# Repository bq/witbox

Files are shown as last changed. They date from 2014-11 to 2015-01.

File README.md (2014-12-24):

Witbox
======

In this repository you will find the source files for the [bq Witbox 3D printer](http://www.bq.com/es/productos/witbox.html). If you are missing something, please do not hesitate to [file an issue on github](https://github.com/bq/witbox/issues).

# License 

Witbox is licensed under a [Creative Commons Attribution-ShareAlike 4.0 International License](http://creativecommons.org/licenses/by-sa/4.0/)

Please read the LICENSE file for more details.

Directory structure
===================

 * `autodesk-inventor`: The original Witbox source files for Autodesk Inventor(tm) and the exported step file. This folder is frozen. Find the latest version in the `freecad` folder

 * `freecad`: Witbox source files in [FreeCAD](http://www.freecadweb.org/). This is a work in progress. All the original files are being migrated to Freecad (see below)

 * `Witbox-BOM.ods`: Witbox Bill of Materials. Document for [LibreOffice](https://www.libreoffice.org/).

**Please note**: The original Witbox design was made in Autodesk Inventor(tm) which is proprietary software. Since we love open formats we are migrating the Witbox parts to [FreeCAD](http://www.freecadweb.org/), which is a multiplatform open source CAD software. We invite people from the community to join us and help us to complete the task.

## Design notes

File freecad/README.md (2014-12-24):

Open Format
===========

In this repository you will find the source files of the [bq witbox 3D printer](http://www.bq.com/gb/products/witbox.html) migrated to [FreeCAD](http://www.freecadweb.org/). This migration is an ongoing work in progress, but if you are missing something specific, please do not hesitate to [file an issue on github](https://github.com/bq/witbox/issues).

Directory structure
===================

There are two folders:

* `native-freecad`: contains the Witbox parts in FreeCAD's native .fcstd format
* `exports`: contains exports of the parts generated from the FreeCAD source files
  * `stl`: Parts exported to STL format
  * `step`: Parts exported to STEP format

Work in progress
================

We are migrating the Witbox parts from Autodesk Inventor to FreeCAD. Currently only a few parts have been migrated. We invite people from the community to join us and help us to complete the task.

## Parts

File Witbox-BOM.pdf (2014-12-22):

## Witbox BOM

Part Number | Description | Quantity | Units | Comments
C04H030029 | XY Support | 1 PCs | | 2mm metal sheet
C04H020006 | Bearing MF105zz (5x10x4) | 8 PCs
C04H030014 | Rear rod drive Ø5 – 487mm | 1 PCs
C04H030017 | Front rod drive Ø5 – 50mm | 2 PCs
C04H020003 | GT2 Pulley 20 teeth | 7 PCs
C04H020014 | Y Belt -- GT2 2MR-280 | 1 PCs
C04H020015 | Y Belt -- GT2 2MR-696 | 2 PCs
C04H010011 | Nema17 Motor, 12VDC, 4000g.cm | 3 PCs | | PTFE
C04H030034 | X Motor Support | 1 PCs | | 3mm metal sheet
C04H030030 | X carriage | 1 PCs | | 2mm metal sheet
C04H030031 | X-end-motor | 1 PCs | | 2mm metal sheet
C04H030032 | X-end | 1 PCs | | 2mm metal sheet
05BQMEC005 | Linear Ball Bearing LM8uu | 8 PCs
C04H010003 | Mechanical Endstop | 3 PCs | | x,y and z axes
C04H030023 | Plastic Support Endstop | 3 PCs
C04H020027 | X-Ends Chain pair | 1 PCs | | (male and female ends)
C04H020029 | Y-Ends Chain pair | 1 PCs | | (male and female ends)
C04H030015 | Y smooth rod Ø8 – 360mm | 2 PCs
C04H030016 | X smooth rod Ø8 – 380mm | 2 PCs
C04H020016 | X Belt-GT2 2MR-848 | 1 PCs
C04H030019 | X-axis idler pulley | 1 PCs
C04H030018 | X-axis idler pulley shaft | 1 PCs
C04H030012 | X-axis idler pulley support | 1 PCs
C04A100003 | Witbox extruder sticker | 1 PCs
C04H050002 | Setscrew M4x5 ISO 4026/DIN-913 | 19 PCs | | Pulleys, linear bearings
C04H050009 | Bolt M4 x 6 DIN 7984 | 34 PCs
C04H050017 | Bolt M3 x 6 ISO 7380 | 23 PCs
G003286 | Led strip with wires | 1 PCs
C04H040005 | Pneumatic tube Ø8 | 0.079 m | | 3 parts (covers for drive bars)
C04H030024 | Air nozzle | 1 PCs | | PLA printed part
C04H020035 | MK7 Drive Gear for 1.75mm | 1 PCs
C04H030009 | Lever extruder | 1 PCs
C04H020008 | Bearing 623ZZ (3x10x4) | 1 PCs
C04H040004 | PTFE Tube Ø4 | 0.02 m | | Hotend
C04H010008 | B57560G104F 100k Thermistor | 1 PCs
C04H010033 | 40w Ceramic Cartridge Heater | 1 PCs
C04H030096 | Extruder motor support | 1 PCs
C04H020019 | Extruder spring 16mm Ø4 Ø0.6 | 1 PCs
C04H020001 | Extruder Heat Sink (40x40x11) | 1 PCs
C04H010006 | Brushless DC Cooling Fan - RD4010B12H | 1 PCs
C04H030033 | Blower support | 1 PCs | | 2mm metal sheet
C04H010007 | DC Blower Fan RB5015B12M+ 40 mm wire – JST male connector 2.5mm pitch | 1 PCs
C04H040001 | Rotatory Pneumatic fitting | 1 PCs
C04H030010 | Fibonacci Support | 1 PCs
C04H040002 | Pneumatic fitting QSMS-4 | 1 PCs
C04H050001 | Setscrew M3x4 ISO 4026/DIN-913 | 3
C04H050004 | dowel pin Ø3x20 – ISO-2338/DIN-7 | 1 PCs
C04H050005 | Bolt M3x12 – ISO-10642/DIN-7991 | 1 PCs
C04H050007 | Bolt M3x6 – ISO-10642/DIN-7991 | 42 PCs
C04H050009 | Bolt M4 x 6 DIN 7984 | 6 PCs
C04H050012 | Bolt M3x14 - ISO- 4762/DIN-912 | 1 PCs
C04H050013 | Bolt M3x18 - ISO- 4762/DIN-912 | 2 PCs

C04H050014 | Bolt M3x20 - ISO- 4762/DIN-912 | 2 PCs
C04H050015 | Bolt M3x22 - ISO- 4762/DIN-912 | 4 PCs
C04A010001 | Black Strap 50X2.5x190 | 2 PCs
C04H040003 | PTFE tube | 1.38 m | Fibonacci
G003287 | Cable chain | 1
C04H030022 | Fitting ferrule | 1 PCs
C04H030045 | Metal sheet base 1.5mm | 1 PCs
C04H010010 | Power Supply S350-12 AC | 1 PCs
C04H010014 | BULGIN BZM27/Z0000/57B | 1 PCs
C04H010002 | Smart LCD controller | 1 PCs
G004085 | Display Housing | 1 PCs
C04H010005 | Brushless DC Cooling Fan – RD5010B12H | 2 PCs
C04H030046 | Electronic metal sheet cover 1.5mm | 1 PCs
C04H010001 | Ramps 1.4 Kit | 1 PCs
C04H010020 | Stepstick Drivers A49988 4 layers | 4 PCs
C04H030013 | Control Knob | 1 PCs
C04H020013 | Hinge | 2 PCs
C04H030047 | Hinge supplement | 2 PCs
C04H050003 | Setscrew M5x8 Iso - 4026/Din - 913 | 1 PCs | Control Knob
C05I070037 | M8x20 Screw ISO 7380 - ZN | 2 PCs
C04H050022 | M4.2 x 16 ISO 7380 | 4 PCs
C04H050025 | M5 Nut DIN-934 | 8 PCs
C04H050021 | Screw 2.9 x 8 | 4 PCs
C04H030057 | Plastic Support Fan 50 | 2 PCs
C04H030026 | Arduino plastic base | 1 PCs
C04H030040 | Left Corner Metal Sheet | 1 PCs
C04H010012 | Nema17 Motor, 12VDC, 4800g.cm | 1 PCs | Y axis
C04H030035 | Y Motor support | 1 PCs | 3mm metal sheet
C04H020009 | Flexible Shaft Z Coupling 5mm/8mm | 1 PCs
C04H030048 | Motor Z support | 1 PCs | 3mm metal sheet
C04H020024 | Lead Screw Z Axis 2mm pitch | 1 PCs
C04H020023 | Screw Drive SWZ-W-104003 | 1 PCs
C04H030036 | Y Mechanical Endstop Support | 1 PCs
C04H030081 | Bed metal support | 1 PCs | 2mm metal sheet
C04H030041 | Z carriage | 1 PCs | 2mm metal sheet
C04H020018 | Spring Ø6 Ø0.8 30mm | 3 PCs | Bed
C04H030044 | Rear metal sheet | 1 PCs | 2mm metal sheet
C04H010004 | Brushless DC Cooling Fan - RD8025B12H | 2 PCs | Rear fans
C04H020020 | Linear guide, NS-01-27-AR | 2 PCs
C04H020021 | Guide carriage | 2 PCs
C04H020022 | Preloaded Guide carriage | 2 PCs
C04H030021 | Linear guide union | 2 PCs
C04H030090 | Rubber seal 130 x 4 mm for printing bed | 1 PCs
C04H050008 | M4 x 30 bolt – DIN – 6912 | 4 PCs
C04H050023 | | 8 PCs
C04A010001 | Black Strap 50X2.5x190 | 3 PCs
G003266 | Fan 80 wires (left) | 1 PCs
G003267 | Fan 80 wires (right) | 1 PCs
C04H030042 | Z carriage B | 1 PCs
C04H020011 | Spring Knob DIN 467 | 3 PCs
C04H030049 | Z Bearing Support | 1 PCs
C04H020007 | MF88ZZ (8x16x5) Bearing | 1 PCs
C04H020006 | MF105zz (5x10x4) Bearing | 1 PCs

Screw 4.8x9.5 - ISO - 4762/DIN-912 REF. 15x491009ZNI(LOTU)

C04H030039 | Right Corner Metal Sheet | 1 PCs
C04H030027 | Back Cover PVC | 1 PCs
C04H050011 | M6x10 bolt – ISO-7380 | 1 PCs
C04H030054 | Front Cover | 1 PCs
C04H030055 | Left Cover | 1 PCs
C04H030056 | Right Cover | 1 PCs
C04A010001 | Black Strap 50X2.5x190 | 1 PCs
C04H020012 | Lock | 1 PCs
C04H030037 | Metal Sheet Cover Corner | 1 PCs
C04H030038 | Metal Sheet Cover Corner (short) | 1 PCs
C04H030051 | Lateral Protection | 2 PCs | 2mm acrylic
C04H030052 | Superior Protection | 1 PCs
C04H020010 | M3 Thumb Screw | 4 PCs
C04H010015 | SCHURTER 6003.0215 - Cable | 1 PCs
C04H030050 | Spool holder | 1 PCs
C04H010016 | USB Cable 1.8m A-B | 1 PCs
C04H030092 | Witbox black Crystal bed with magnets | 1 PCs
C04H030026 | ramps-plastic-suport | 1 PCs
C04H030020 | hotend short metal tube | 1 PCs
C04H030091 | Acrylic support for bed 85 x 175 mm | 1 PCs
C04H020004 | 0.4 nozzle | 1 PCs
C04H030053 | Acrylic door | 1 PCs
C04H030093 | Hotend heat core unibody | 1 PCs
C04H030094 | Hotend heat core unibody cover | 1 PCs
C04H030007 | Hotend main tube | 1 PCs
C04H030011 | Hotend heater block | 1 PCs

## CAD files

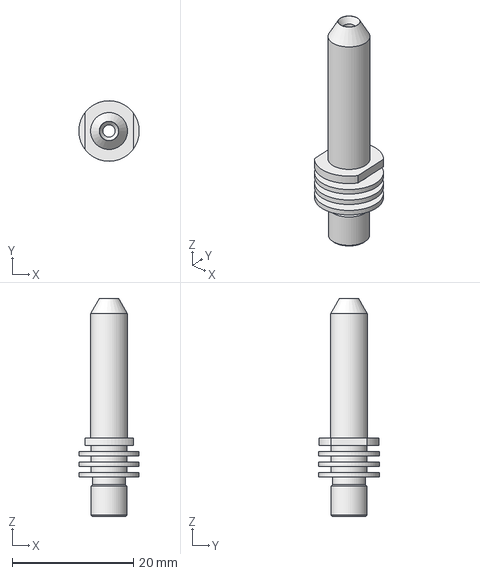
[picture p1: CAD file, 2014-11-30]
freecad/exports/step/hotend-main-tube.step
9.99 x 10.00 x 36.0 mm

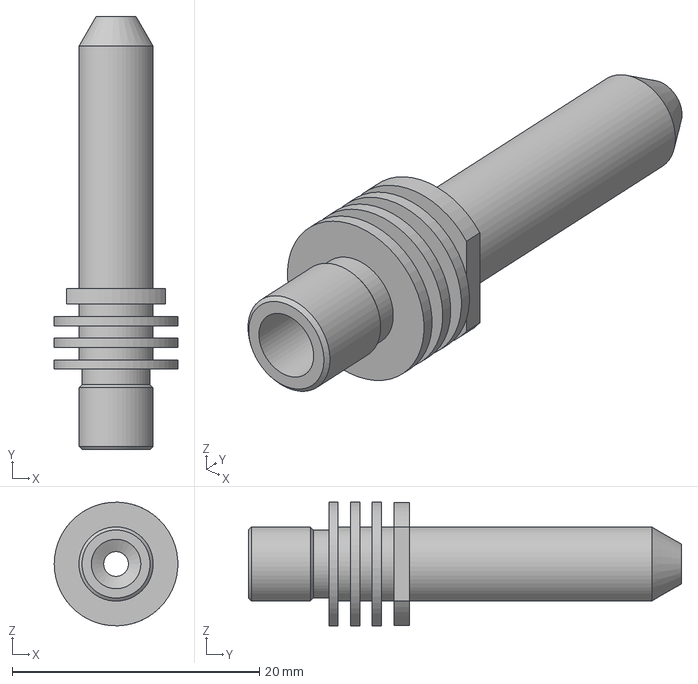
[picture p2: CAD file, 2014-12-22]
autodesk-inventor/step/C04H030007-Hotend-main-tube.stp
9.99 x 35.0 x 10.00 mm

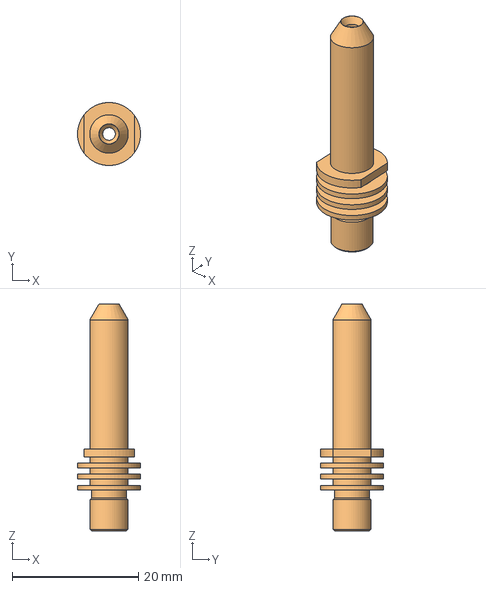
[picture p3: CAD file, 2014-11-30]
freecad/native-freecad/Hotend-main-tube.fcstd
9.99 x 10.00 x 36.0 mm
cutout-1
Hotend-main-tube-final

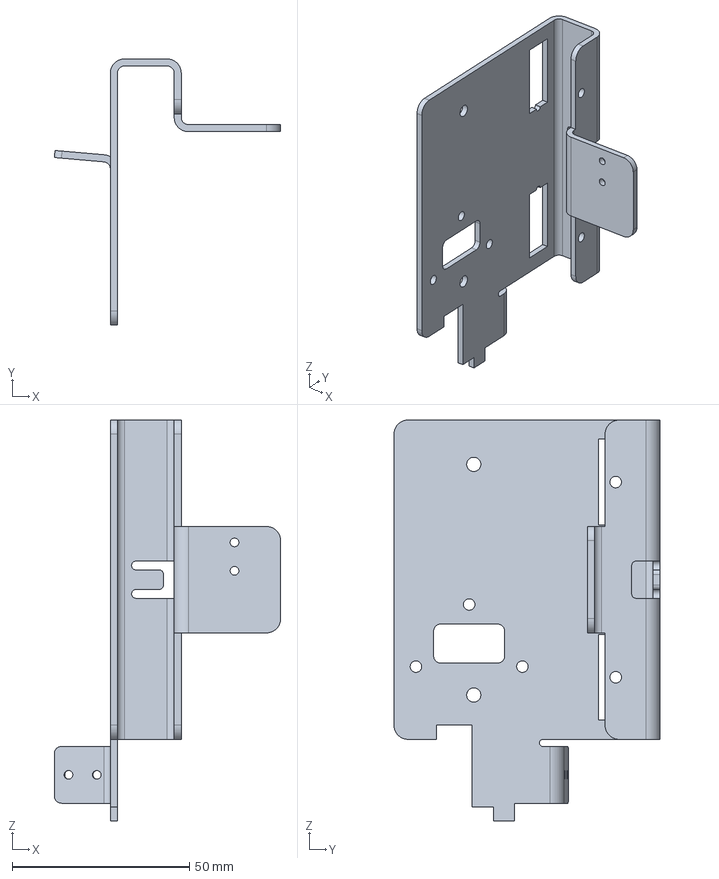
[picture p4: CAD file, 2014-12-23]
autodesk-inventor/step/C04H030031-x-end-motor.stp
63.8 x 75.0 x 113.0 mm

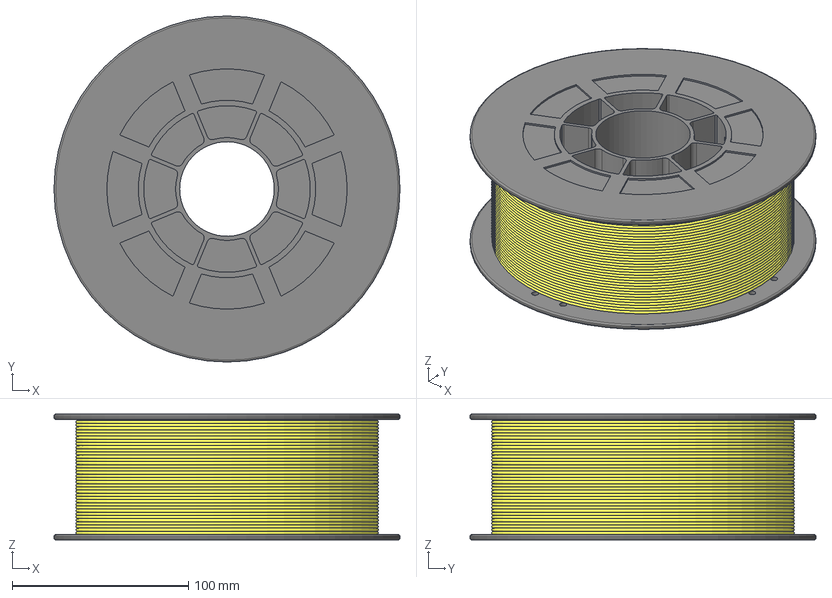
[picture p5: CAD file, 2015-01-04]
freecad/exports/step/yellow-pla.step
196.4 x 196.4 x 71.5 mm

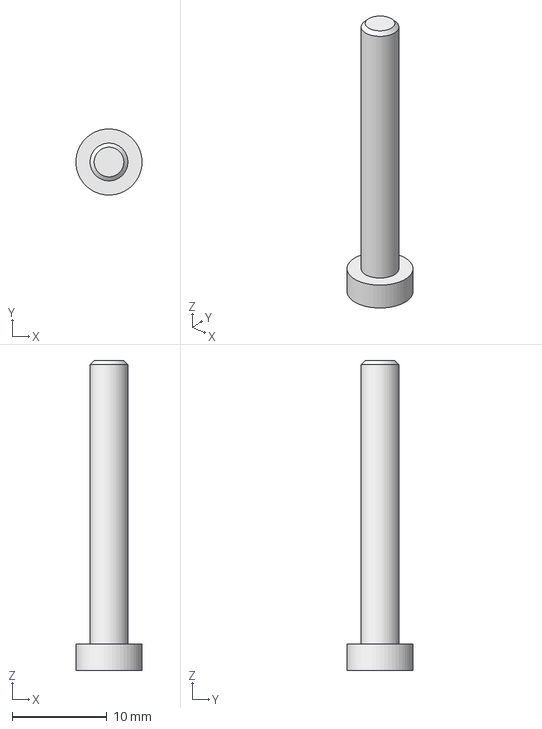
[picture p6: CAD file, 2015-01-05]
freecad/native-freecad/38. TORNILLO M4X30.FCStd
6.99 x 7.00 x 32.8 mm

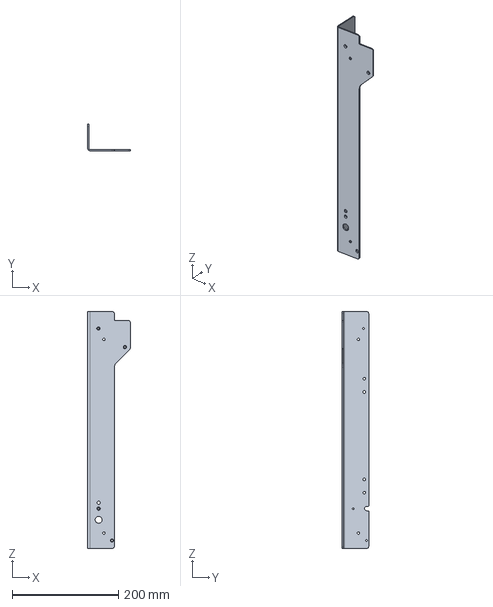
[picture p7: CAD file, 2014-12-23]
autodesk-inventor/step/C04H030040-left-corner-metal-sheet.stp
80.0 x 50.0 x 446.0 mm

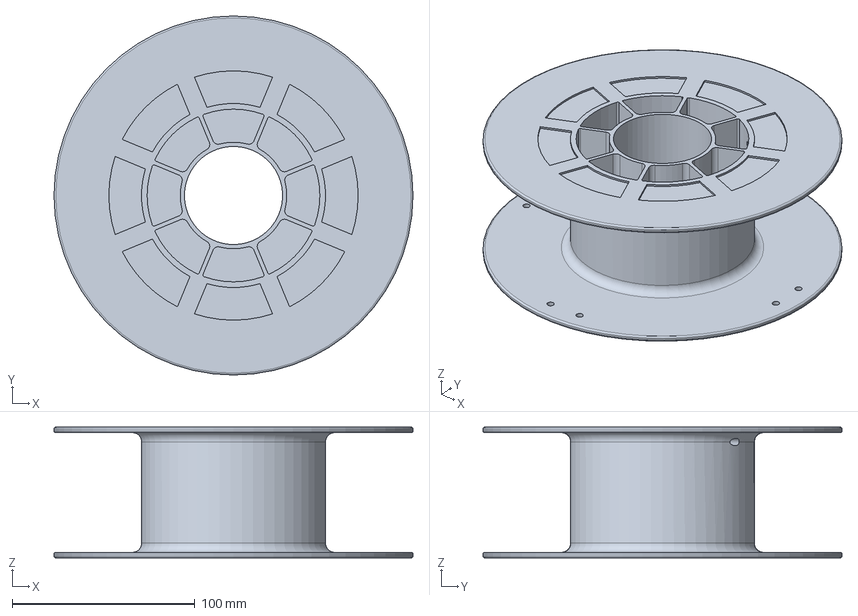
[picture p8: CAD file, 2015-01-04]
freecad/exports/step/pla-reel.step
196.4 x 196.4 x 71.5 mm

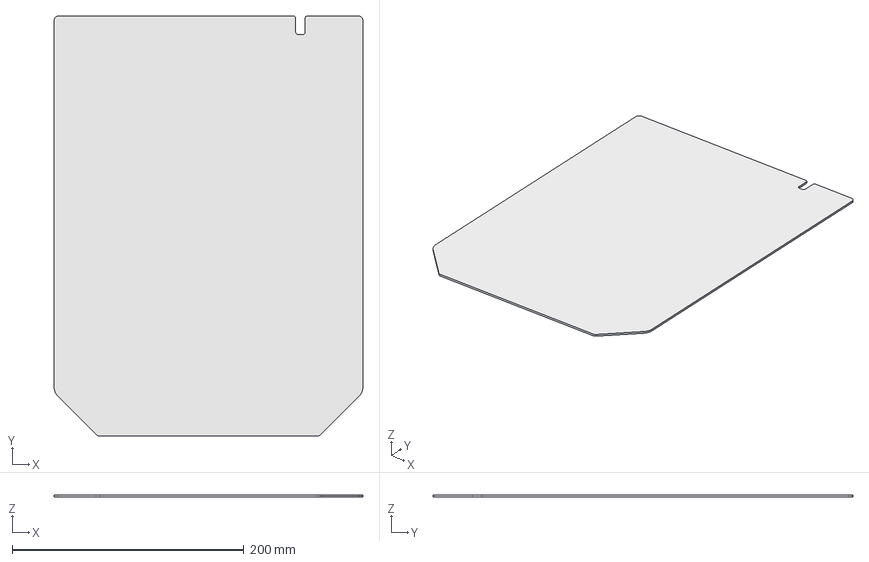
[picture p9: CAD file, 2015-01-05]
freecad/native-freecad/9. POLICARBONATO LATERAL (IZ Y DE).FCStd
266.6 x 362.5 x 2.00 mm

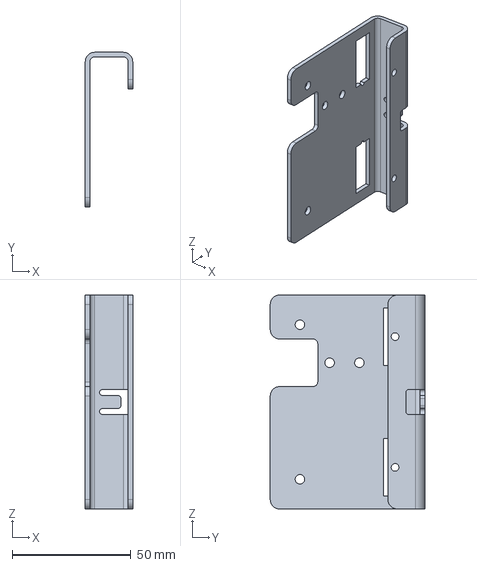
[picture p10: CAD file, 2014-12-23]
autodesk-inventor/step/C04H030032-x-end.stp
20.0 x 65.0 x 90.0 mm

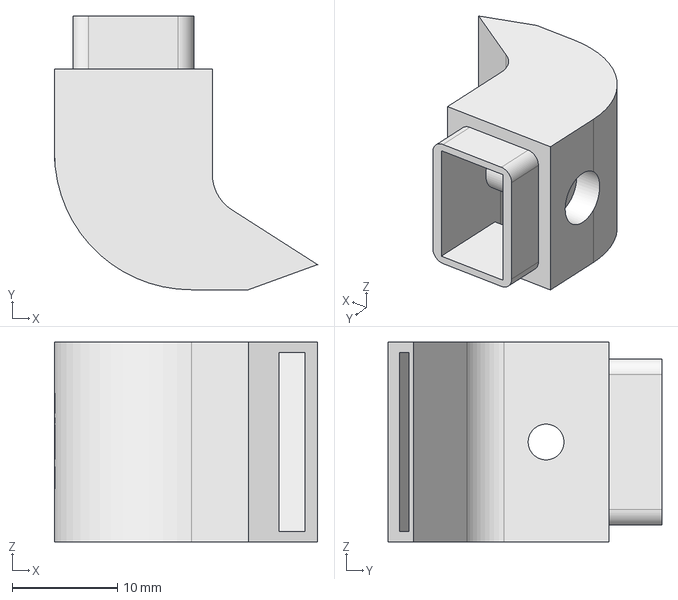
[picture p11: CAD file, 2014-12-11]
freecad/exports/step/extruder-air-nozzle.step
25.0 x 26.0 x 19.0 mm

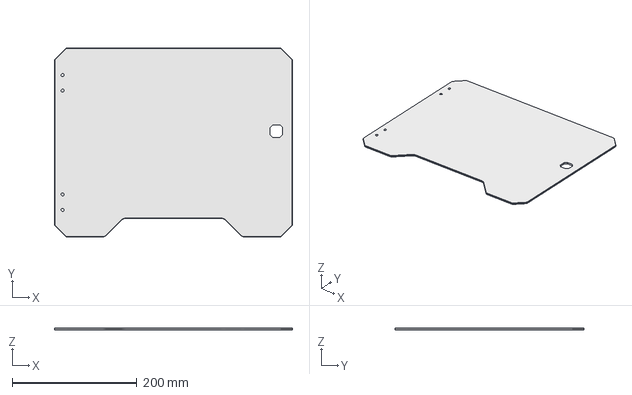
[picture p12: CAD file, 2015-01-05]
freecad/native-freecad/10. PUERTA POLICARBONATO (FRONTAL).FCStd
382.0 x 303.5 x 3.00 mm

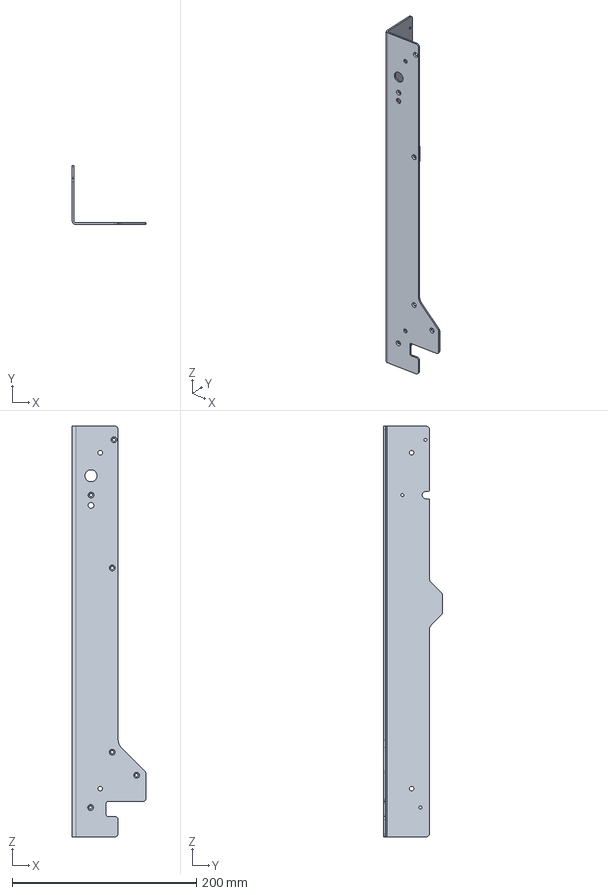
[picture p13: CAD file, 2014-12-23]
autodesk-inventor/step/C04H030039-right-corner-metal-sheet.stp
80.0 x 64.0 x 446.0 mm

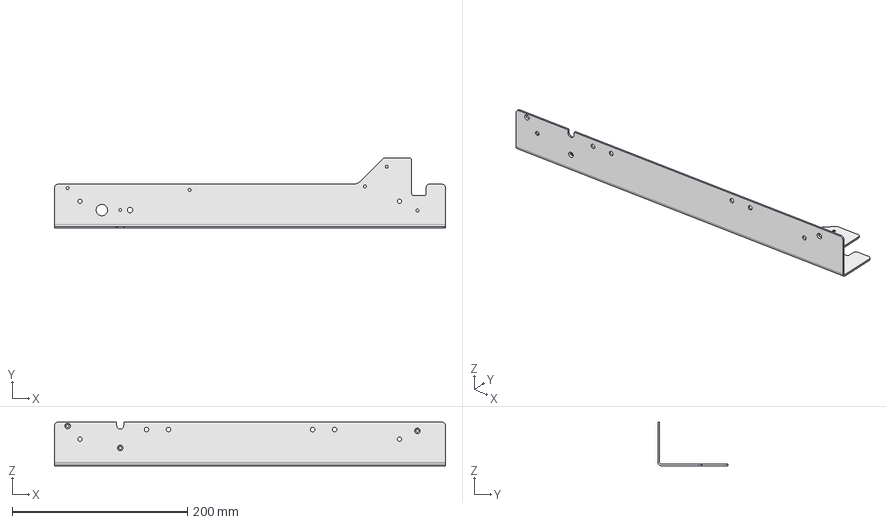
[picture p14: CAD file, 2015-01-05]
freecad/native-freecad/12. ESQUINA MARCO INTERIOR 001 (MIRROR) (SIN LLAVE).FCStd
446.0 x 80.0 x 50.0 mm

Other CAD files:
freecad/exports/step/extruder-air-nozzle-with-support.step
autodesk-inventor/step/C04H030015-y-smooth-bar.stp
freecad/exports/step/extruder-heat-sink.step
freecad/native-freecad/24. SUPLEMENTO RAMPS.FCStd
autodesk-inventor/native-inventor/C04H010008-Thermistor.ipt
autodesk-inventor/native-inventor/C04H010008-Thermistor_v05.ipt
autodesk-inventor/native-inventor/C04H010014-bulgin-BZM27-Z0000-57B.ipt
autodesk-inventor/native-inventor/C04H010033-cartridge-heater-v5.ipt
autodesk-inventor/native-inventor/C04H010033-cartridge-heater.ipt
autodesk-inventor/native-inventor/C04H020001-extruder-heat-sink.ipt
autodesk-inventor/native-inventor/C04H020004-mk7-nozzle_0.4mm.ipt
autodesk-inventor/native-inventor/C04H020009-Flexible-shaft-coupling.ipt
autodesk-inventor/native-inventor/C04H020012-lock.ipt
autodesk-inventor/native-inventor/C04H020024-lead-screw .ipt
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

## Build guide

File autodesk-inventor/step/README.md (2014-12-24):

STEP files generated from Autodesk Inventor 2015
================================================

There are some problems when importing the Witbox-assembly-original_v04.stp file into the current FreeCAD 0.14.

You can find the latest STEP files compatible with FreeCAD at `../../freecad`. There you can also find the sources that have already been converted to FreeCAD.

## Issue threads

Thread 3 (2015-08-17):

Firmware Sources

scipione205, 2015-08-17:
Hi,
I'm using a Witbox and I'm encountering some annoying things with the firmware. Please upload the sources, so we users could participate with the company in improving the printer's performance.

Obijuan, 2015-08-17:
Hi scipione!

You can find the source for the witbox and hephestos firmware in this fork

https://github.com/bq/Marlin

Best regards

scipione205, 2015-08-17:
Thank you Obi Juan! May the force be with you.

Closed 2015-08-17.

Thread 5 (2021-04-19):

FFC Cable

Beltar1989, 2021-04-19:
At our Witbox the FFC Cable of X axis got defect.
I don't find any Partnumber or hint about connector to search for replacement

jvegaf, 2021-04-20:
Hi,

the BQ company does not exist now

did you look at the BOM files in the root of the project? maybe you have a luck

[https://github.com/bq/witbox/blob/master/Witbox-BOM.ods](https://github.com/bq/witbox/blob/master/Witbox-BOM.ods)
[https://github.com/bq/witbox/blob/master/Witbox-BOM.pdf](https://github.com/bq/witbox/blob/master/Witbox-BOM.pdf)

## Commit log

2014-11-23 Initial witbox assembly in Freecad. Imported from the original step file. The z leadscrew and z-coupler are missing
2014-11-23 Extruder body. Migration started
    [Extruder-body.fcstd]
2014-11-23 Witbox assembly: Initial sort of the parts into folders. Not finished
2014-11-23 Extruder body: migrated to freecad. STL and STEP files
    [Extruder-body.fcstd, extruder-body.step, extruder-body.stl]
2014-11-23 Moved to the Freecad-parts-src folder
    [Extruder-body.fcstd]
2014-11-23 Extruder spring added
    [Extruder-spring.fcstd, extruder-spring.step, extruder-spring.stl]
2014-11-30 Extruder spring: thumbnail updated
    [Extruder-spring.fcstd]
2014-11-30 Extruder parts: drive gear, lever, lever pole, hotend main tube
    [Extruder-drive-gear.fcstd, Extruder-lever-pole.fcstd, Extruder-lever.fcstd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]
2014-11-30 Extruder drive gear migrated to freecad
    [Extruder-drive-gear.fcstd, extruder-drive-gear.step, extruder-drive-gear.stl]
2014-11-30 Extruder lever migrated to freecad
    [extruder-lever-pole.step, extruder-lever-pole.stl, extruder-lever.step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]
2014-11-30 hotend main tube: stl and step files
    [hotend-main-tube.step, hotend-main-tube.stl]
2014-11-30 Hotend main tube: thumbnail updated
    [Hotend-main-tube.fcstd]
2014-12-04 Freecad folder moved to the new sources folder
    [Extruder-body.fcstd, Extruder-drive-gear.fcstd, Extruder-lever-pole.fcstd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]
2014-12-04 Step folder moved to Sources/Freecad/Step
    [extruder-body.step, extruder-drive-gear.step, extruder-lever-pole.step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]
2014-12-04 stl folder moved to Sources/Freecad
    [extruder-body.stl, extruder-drive-gear.stl, extruder-lever-pole.stl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]
2014-12-04 Template file for the Witbox Bill of materials
2014-12-05 new freecad/native-freecad folder. New CONTRIBUTE.md. New BOM.md
    [Extruder-body.fcstd, Extruder-drive-gear.fcstd, Extruder-lever-pole.fcstd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]
2014-12-05 Sources/Freecad/step folder moved to freecad/exports/step
    [extruder-body.step, extruder-drive-gear.step, extruder-lever-pole.step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]
2014-12-05 Sources/Freecad/stl moved to freecad/exports/stl
    [extruder-body.stl, extruder-drive-gear.stl, extruder-lever-pole.stl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]
2014-12-06 hotend nozzle migrated to freecad
    [hot-end-nozzle.stl, hotend-nozzle.fcstd, hotend-nozzle.step]
2014-12-06 Freecad assembly: hotend parts moved to their own folder
2014-12-06 Hotend short metal tube migrated to freecad
    [hotend-short-metal-tube.fcstd, hotend-short-metal-tube.step, hotend-short-metal-tube.stl]
2014-12-06 hotend ptfe tube migrated to freecad
    [hotend-ptfe-tube.fcstd, hotend-ptfe-tube.step, hotend-ptfe-tube.stl]
2014-12-06 hotend heater block migrated to freecad
    [hotend-heater-block.fcstd, hotend-heater-block.step, hotend-heater-block.stl]
2014-12-07 Hotend heater cartridge migrated to freecad. First draft. Not finished
    [hotend-heater-cartridge-connector.fcstd, hotend-heater-cartridge.fcstd]
2014-12-07 hotend heater cartridgeand thermistor
    [hotend-heater-cartridge.fcstd, hotend-thermistor-connector.fcstd, hotend-thermistor.fcstd]
2014-12-07 Extruder setcrew migrated to freecad
    [extruder-setscrew1.fcstd]
2014-12-08 Extruder blower support migrated to freecad
    [Extruder-blower-support.fcstd]
2014-12-08 Parts exportes to step and stl
    [extruder-blower-support.step, extruder-blower-support.stl, extruder-setscrew1.step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]
2014-12-08 Extruder heat sink migrated to freecad
    [extruder-heat-sink.fcstd, extruder-heat-sink.step, extruder-heat-sink.stl]
2014-12-11 Air nozzle: exported to stl and step files. With and without support
    [extruder-air-nozzle-with-support.step, extruder-air-nozzle-with-support.stl, extruder-air-nozzle.fcstd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]
2014-12-16 Witbox freecad assembly changed
2014-12-18 Initial BOM. Work in progress. Parts of the xy axes
    [Witbox-BOM.ods]
2014-12-18 Witbox bom: more components added
    [Witbox-BOM.ods]
2014-12-22 Witbox BOM finished. Exported to pdf
    [Witbox-BOM.ods]
2014-12-22 Assembly: some name changed
2014-12-22 BOM.md removed. The BOM is located in the file Witbox-BOM.ods
2014-12-22 Witbox-Bom.ods added to README
2014-12-22 Inventor ipt files added (first wave)
    [C04H010008-Thermistor.ipt, C04H010008-Thermistor_v05.ipt, C04H020009-Flexible-shaft-coupling.ipt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]
2014-12-22 All the inventor files added
    [C04H010014-bulgin-BZM27-Z0000-57B.ipt, C04H010033-cartridge-heater-v5.ipt, C04H010033-cartridge-heater.ipt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]
2014-12-22 BOM updated
    [Witbox-BOM.ods]
2014-12-22 File renamed
    [Hotend-heater-block.ipt, rear-metal-sheet.ipt, rear-metal-sheet_004.ipt]
2014-12-22 witbox assembly: names updated
2014-12-22 step files generated from ipt sources
    [C04H010008-Thermistor.stp, C04H010008-Thermistor_v05.stp, C04H010014-bulgin-BZM27-Z0000-57B.stp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]
2014-12-22 Assembly: small bugfixes in the parts names
2014-12-23 Final ipt and step files uploaded
    [C04H030031-x-end-motor.ipt, C04H030031-x-end-motor.stp, C04H030032-x-end.ipt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]
2015-01-04 PLA reel migrated to freecad
    [PLA-Reel.fcstd, pla-reel.step, pla-reel.stl]
2015-01-04 PLA reel: yellow plastic added
    [PLA-Reel.fcstd]
2015-01-04 Yellow pla reel added
    [yellow-pla.step]
2015-01-05 Piezas FreeCAD
    47 Piezas pasadas de formato Step a FreeCAD
    [1. MARCO PRINCIPAL (MARCO EXTERIOR).FCStd, 10. PUERTA POLICARBONATO (FRONTAL).FCStd, 11. ESQUINA MARCO INTERIOR 001 (LLAVE).FCStd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]
